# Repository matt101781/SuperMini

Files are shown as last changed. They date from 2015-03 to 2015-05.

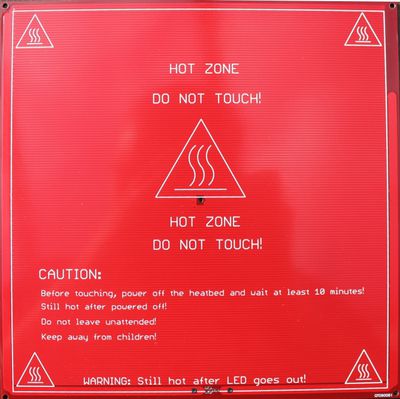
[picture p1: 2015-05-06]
cad/solidworks/decals/400px-PCB_Heatbed_MK2_front_small.jpg

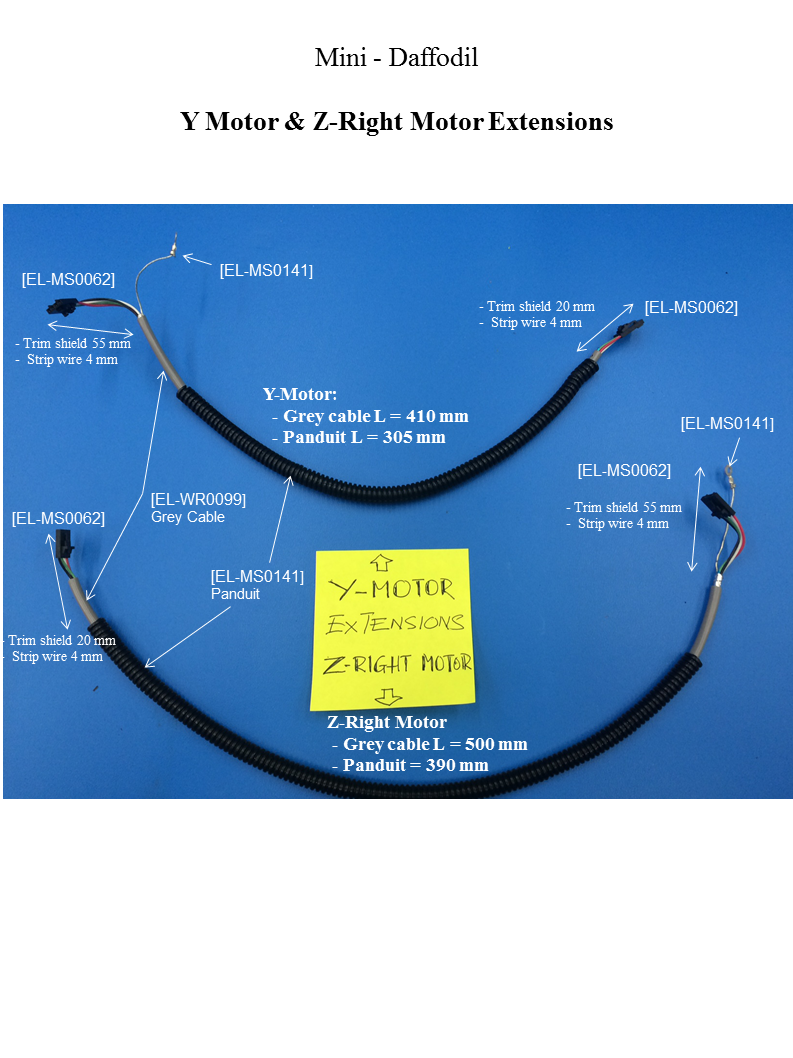
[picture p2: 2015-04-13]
electrical/mini.wire.harnesses/y&z right motor extensions.png

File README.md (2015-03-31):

# SuperMini
Super Mini - Lulzbot Clone

The super mini is a 3D printer based on the Lulzbot Mini.  
Lulzbot is a trademark of Aleph Object Inc.

Differences from the original mini:

- Sheet metal replaced with OpenBeam extruded aluminum frame.
- Bed size increased to 200x200mm.
- Firmware modified for new bed size
- Electronics replaced with TBD board.
- LCD Display added.

All of the printed parts were reused as possible.
COTS components were favored over custom machined items.

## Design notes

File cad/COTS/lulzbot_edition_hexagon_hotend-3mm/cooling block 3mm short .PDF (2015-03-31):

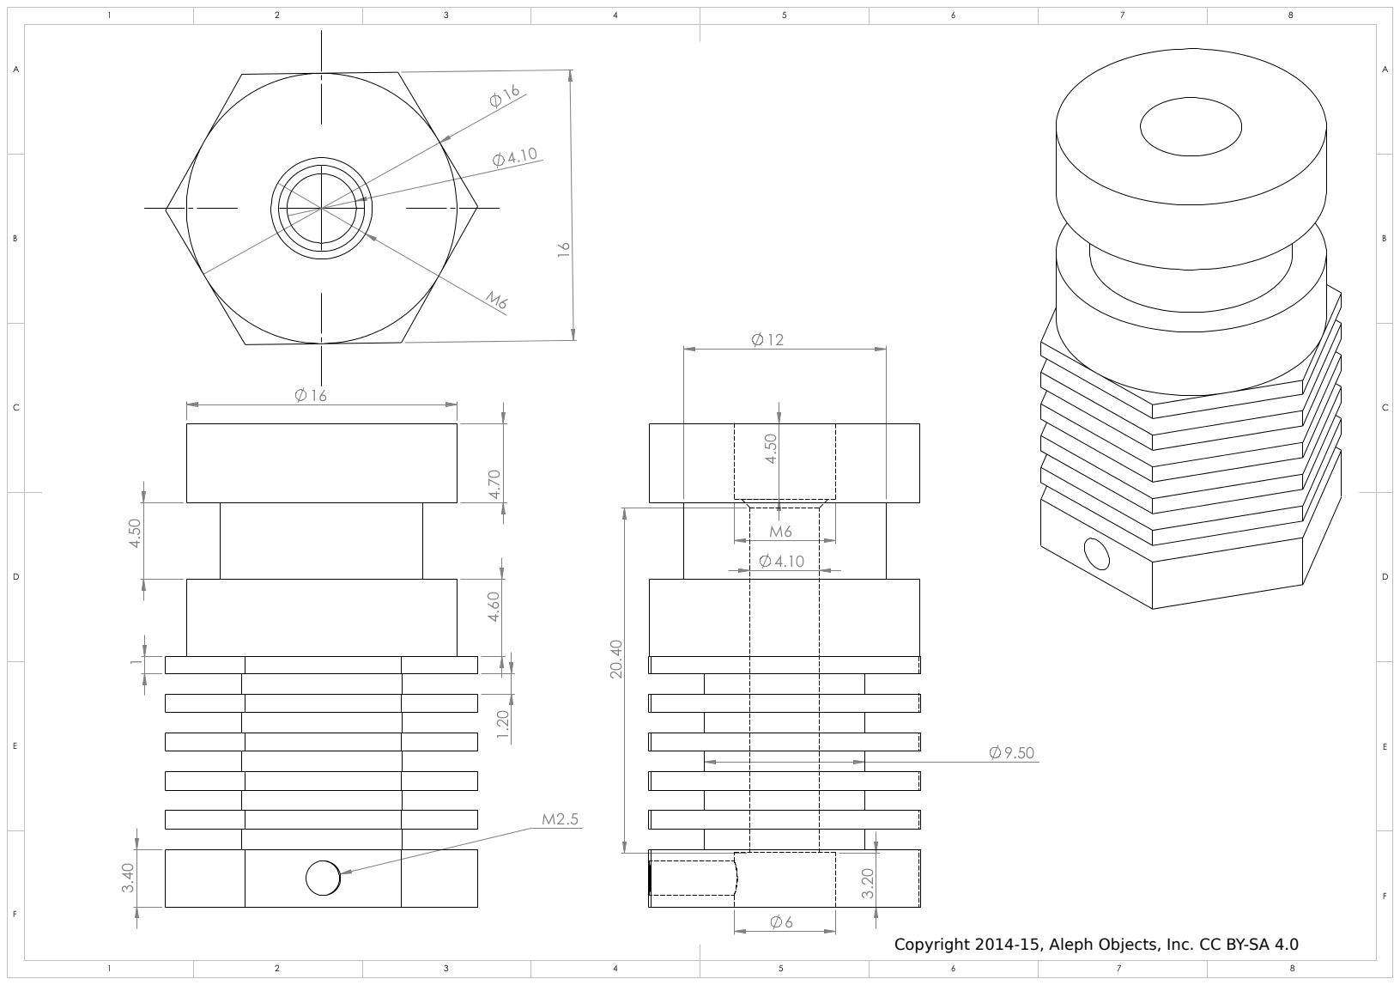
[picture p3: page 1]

Copyright 2014-15, Aleph Objects, Inc. CC BY-SA 4.0

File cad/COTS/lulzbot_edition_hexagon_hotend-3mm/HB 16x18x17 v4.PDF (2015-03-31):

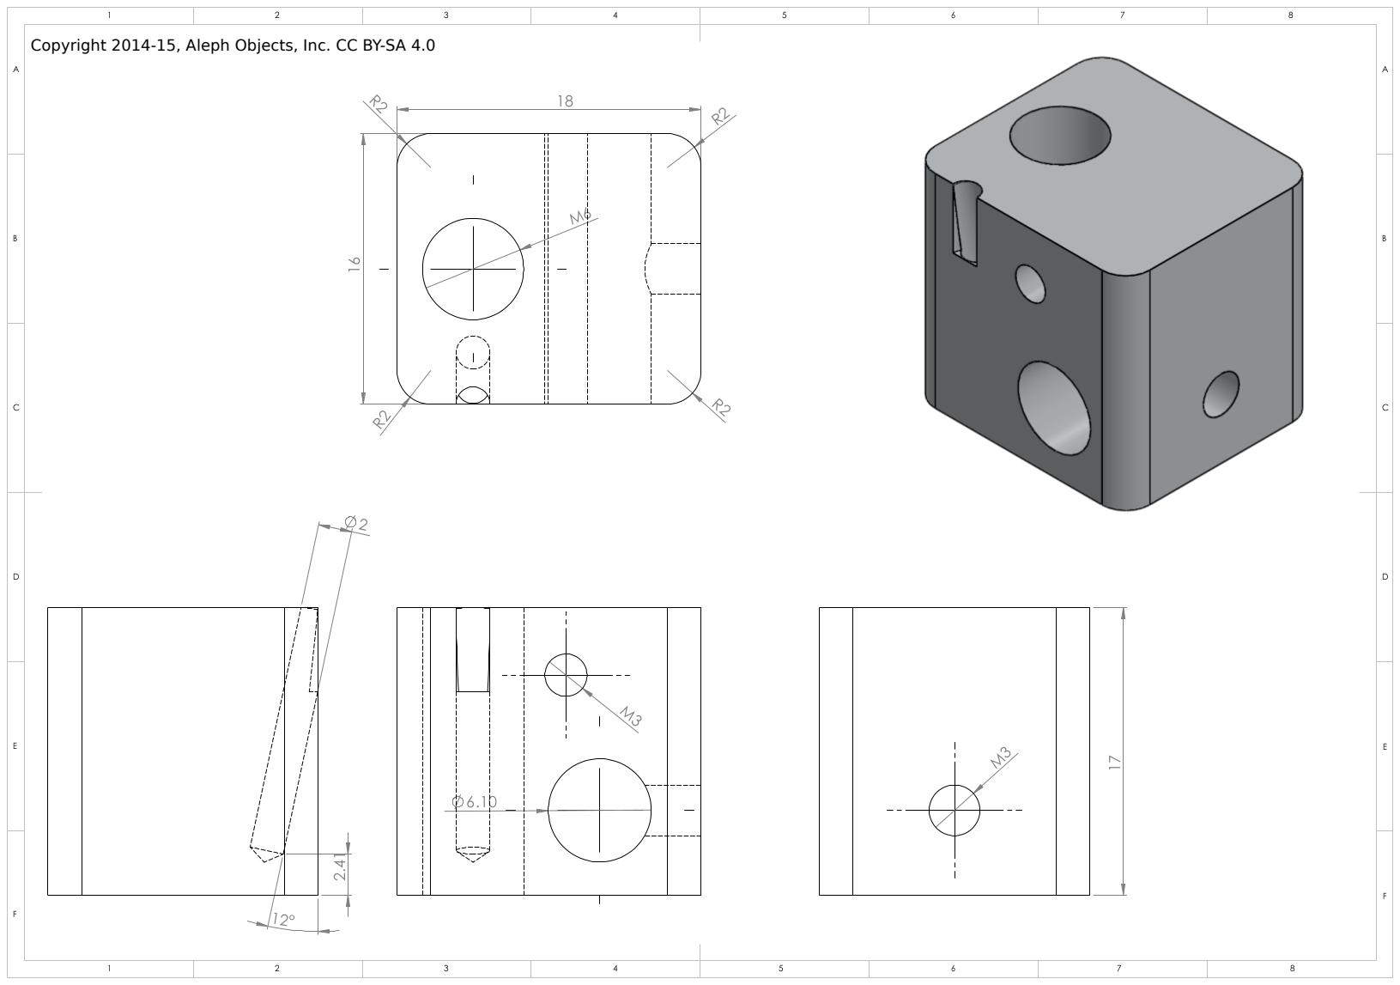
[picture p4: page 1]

Copyright 2014-15, Aleph Objects, Inc. CC BY-SA 4.0

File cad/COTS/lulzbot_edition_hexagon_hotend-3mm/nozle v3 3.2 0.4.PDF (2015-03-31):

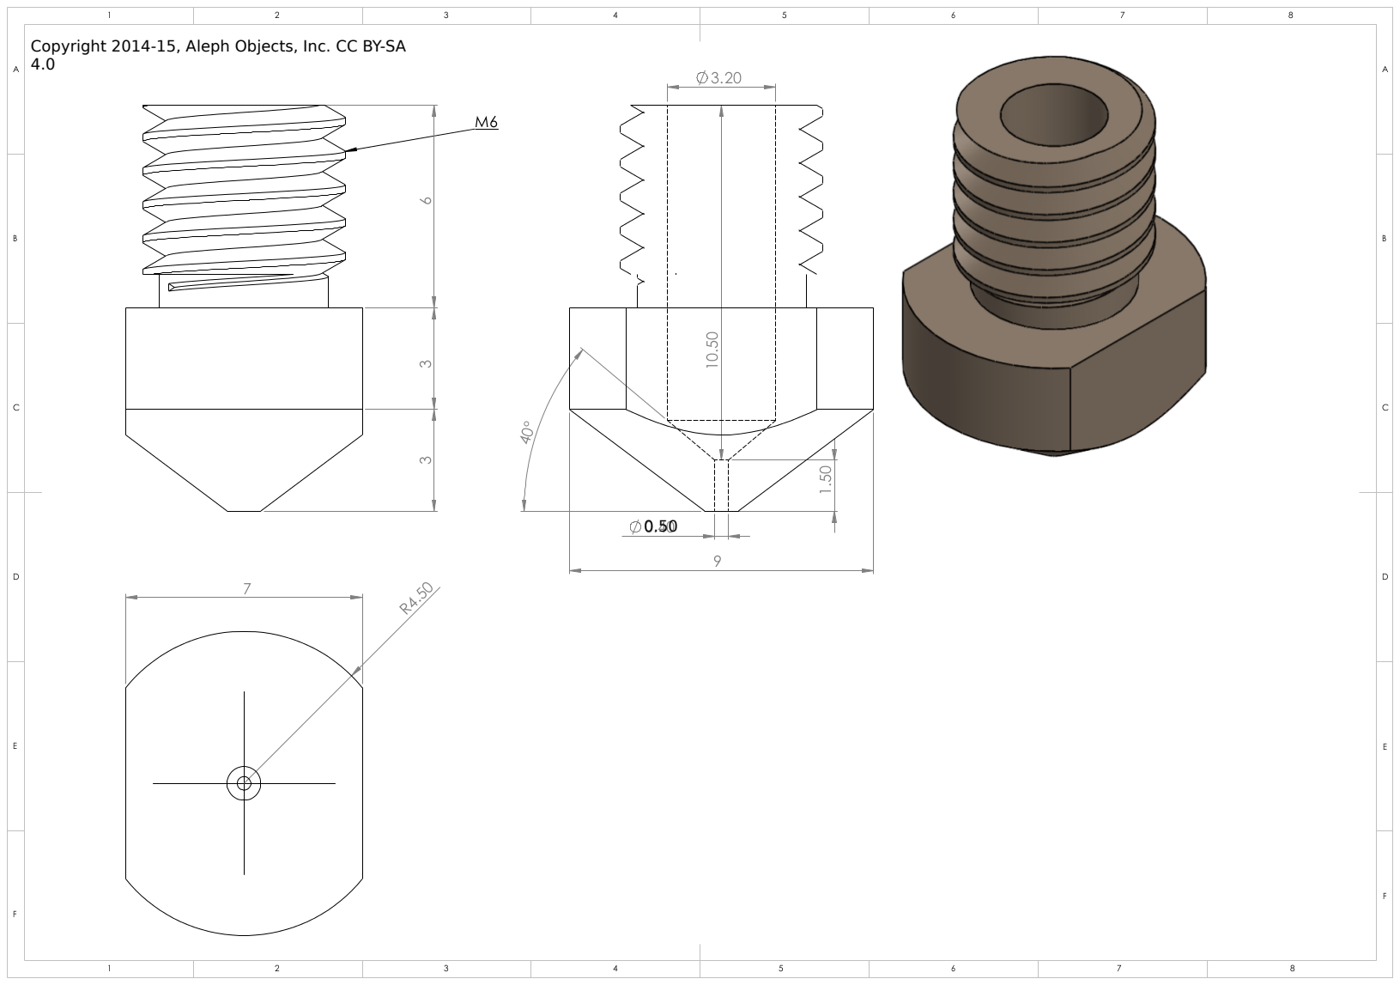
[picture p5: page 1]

0.50

Copyright 2014-15, Aleph Objects, Inc. CC BY-SA 4.0

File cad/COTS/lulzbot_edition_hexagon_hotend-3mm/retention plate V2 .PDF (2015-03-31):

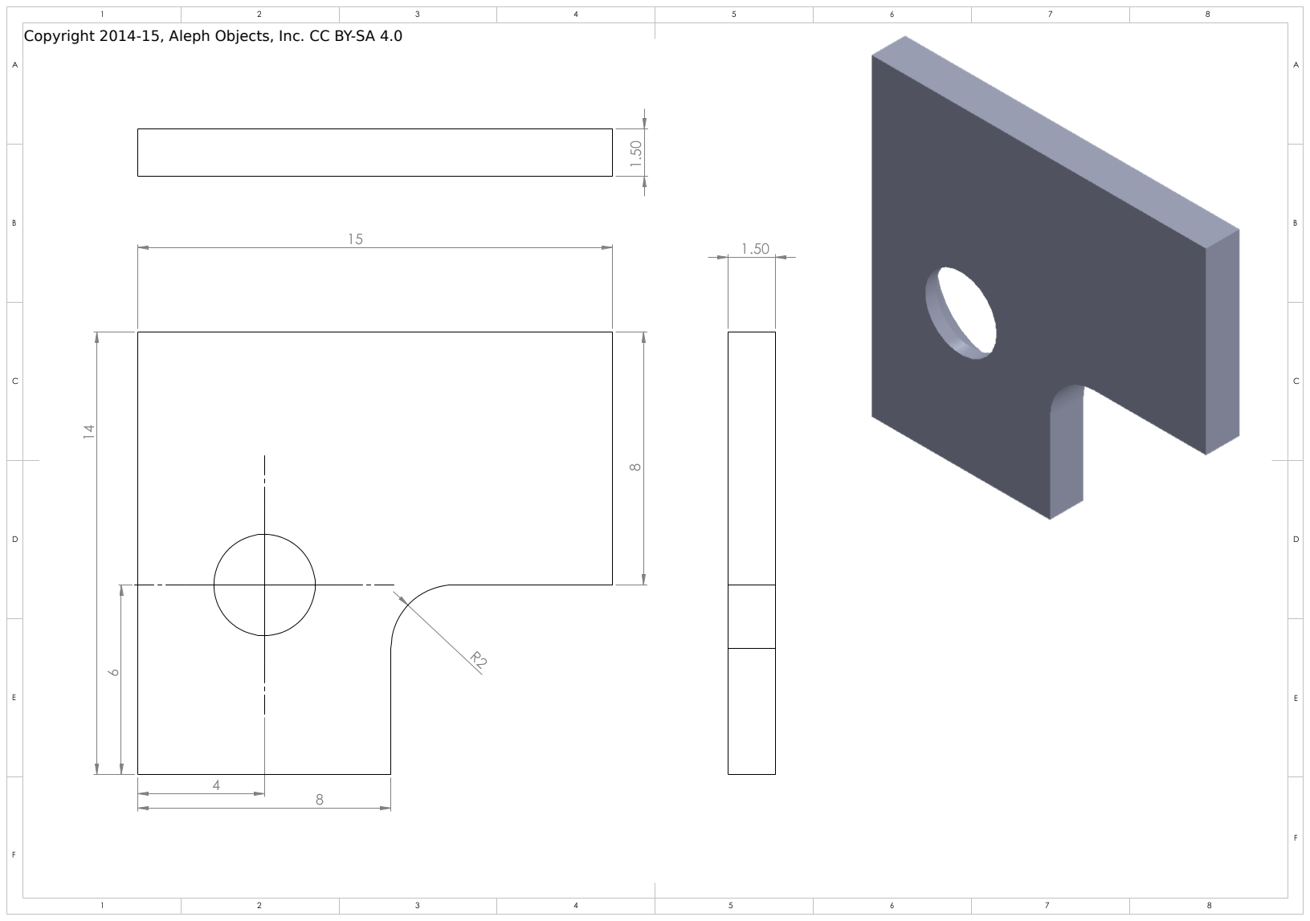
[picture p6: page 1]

Copyright 2014-15, Aleph Objects, Inc. CC BY-SA 4.0

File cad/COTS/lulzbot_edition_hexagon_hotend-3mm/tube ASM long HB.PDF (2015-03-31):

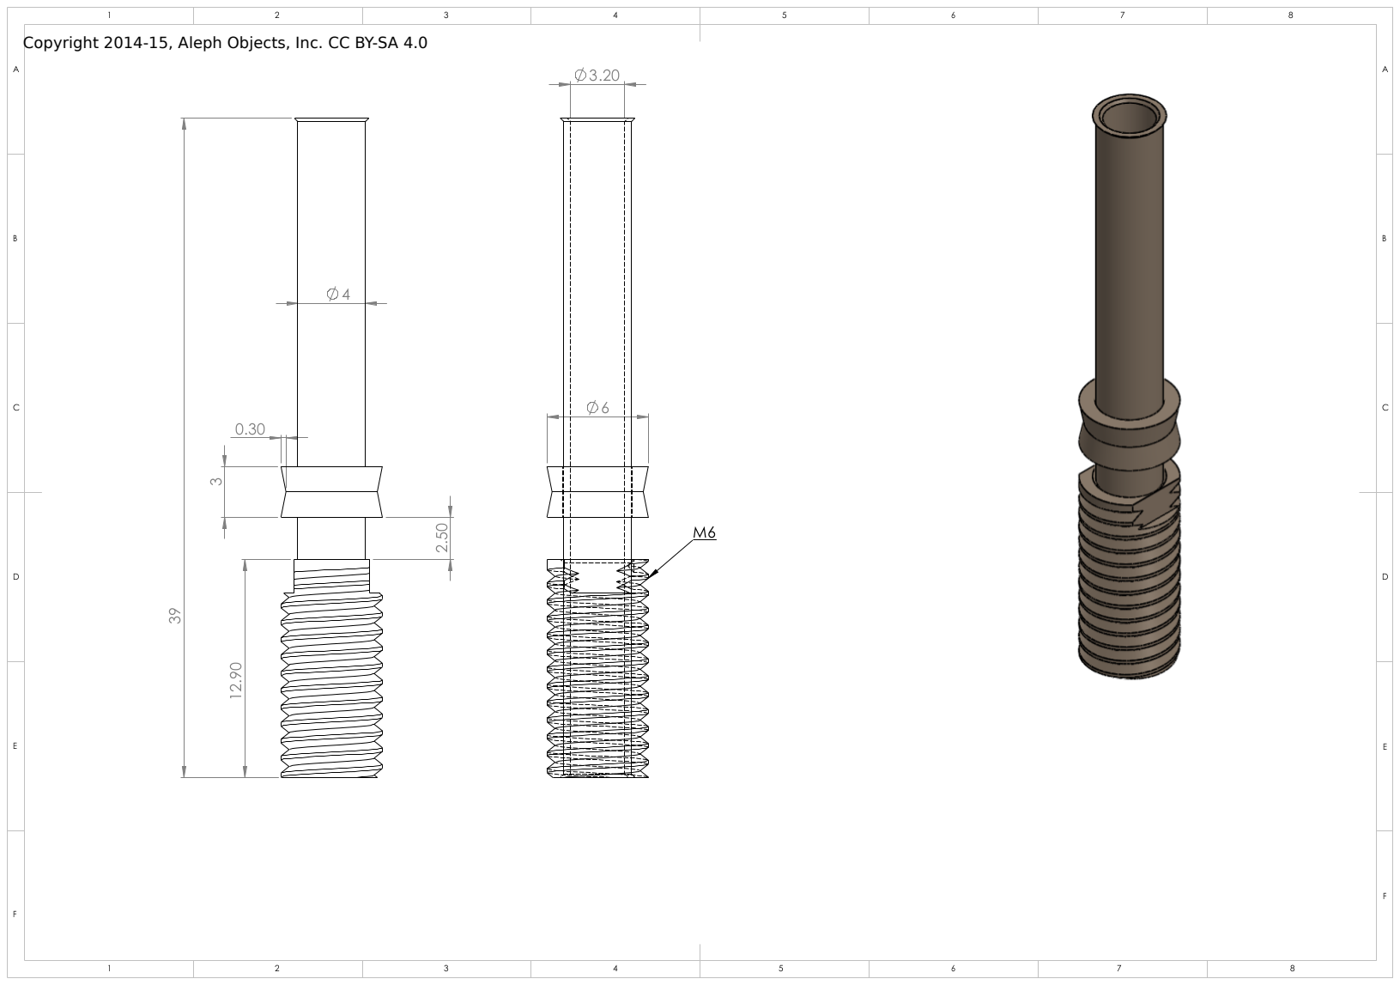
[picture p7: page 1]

Copyright 2014-15, Aleph Objects, Inc. CC BY-SA 4.0

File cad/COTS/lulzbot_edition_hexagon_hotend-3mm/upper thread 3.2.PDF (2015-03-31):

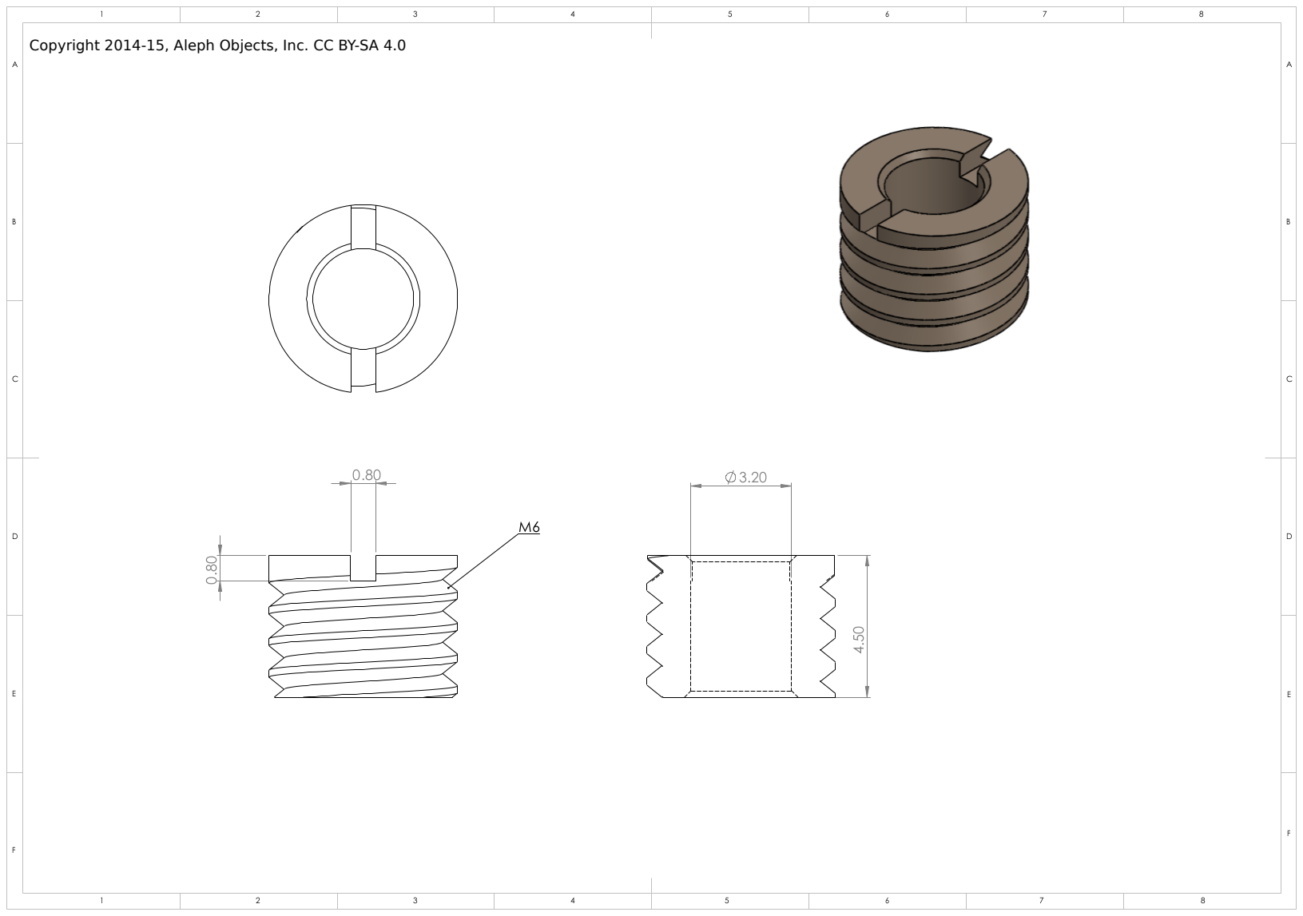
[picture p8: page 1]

Copyright 2014-15, Aleph Objects, Inc. CC BY-SA 4.0

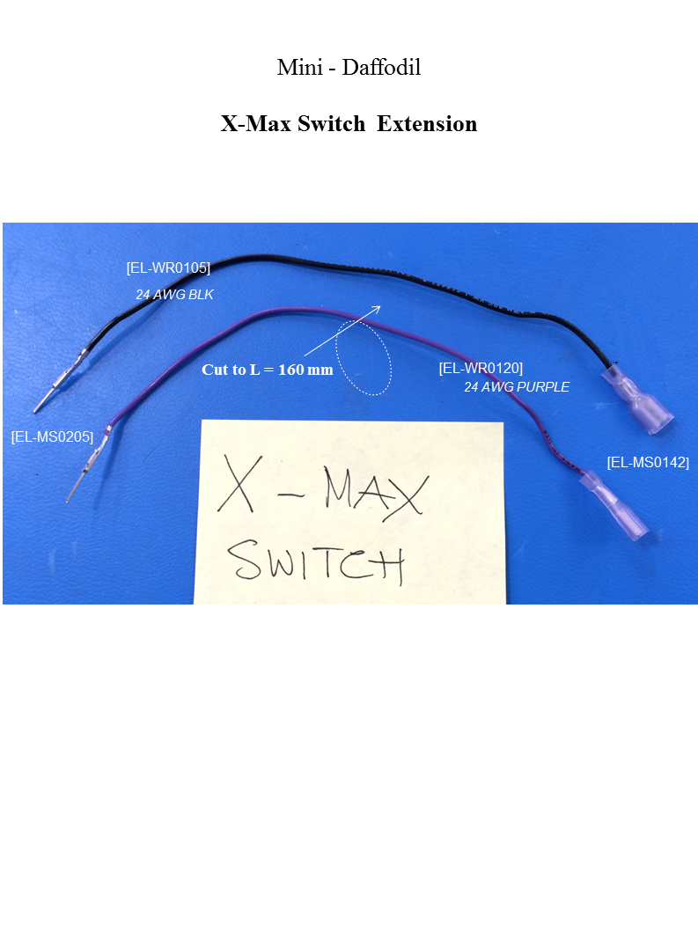
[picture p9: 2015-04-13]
electrical/mini.wire.harnesses/x max.png

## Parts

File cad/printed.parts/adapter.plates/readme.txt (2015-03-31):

Adapter Plates made with Tinkercad.

Links:

blah blah

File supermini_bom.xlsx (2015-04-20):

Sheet: BOM Summary
Supermini BOM Summary

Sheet: Linear Motion
Category | Description | Manufacturer | Manufacturer PN | Web Link | Distributor | Distributor SKU | Qty Per | UOM | My Price | Ext Price | Notes | 1000
Mechanical | DryLin® R - Solid polymer bearing RJM-01, 8mm | IGUS | RJM-01-08 |  | Direct |  | 12 | ea | $4.62 | $55.44 | Upgrade to metal bearings??
Mechanical | 8mm Smooth rod, 315mm, 304 Stainless Steel | Misumi | SSFJ8-315 |  |  |  | 2 | ea | $16.10 | $32.20 | z axis rods
Mechanical | 8mm smooth rod, 355mm, 304 Stainless Steel | Misumi | SSFJ8-355 |  |  |  | 4 | ea | $15.29 | $61.16 | x and y axis rods
Mechanical | Drive Rod 10mm | Misumi | MTSTRW10-287-F22-V7-S7-Q7-FV0-FW10-FY1 |  |  |  | 2 | ea | $56.00 | $112.00 | Get the 7MM version.
Mechanical | 10mm x 2mm Flange mount supernut | Thomson | MTS10x2m |  |  |  | 2 | ea | $25.00 | $50.00
Mechanical | Sealed Skateboard/inline/Rollerblade Skate Bearing Ball Bearings - |  |  |  | vxb.com | Kit6943 | 4 | ea | $2.12 | $8.50 | Kit of 8.
Mechanical | Metric Steel Ball Bearing, Double Sealed Bearing No.627 for 7mm Shaft Diameter |  |  |  | vxb.com |  | 4 | ea |  | $0.00 | These are for the drive rods top and bottom, changing the diameter avoids the need for these
Mechanical | Shaft Coupler 5mm to 7mm | Misumi | CPSX19-5-7 |  |  |  | 2 | ea | $26.00 | $52.00
 | NOTE - Replace 627 bearing at bottom of shaft with 636 bearing that has a 6mm bore. A 5mm to 6mm shaft coupler is then needed. -- THIS MIGHT NOT BE NECESSARY
 |  |  |  |  |  |  |  |  |  | $371.30
 | Check for LME8UU bearings, possible replacements to the poly plastic bearings

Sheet: Bed Assembly
Category | Description | Manufacturer | Manufacturer PN | Web Link | Distributor | Distributor SKU | Qty Per | UOM | My Price | Ext Price | Notes | 1000
Bed | PEI (Polyetherimide) Sheet 12" x 12" |  | ULT-0030-E | Link (http://www.amazon.com/dp/B0013HKZTA/ref=biss_dp_t_asn) | Amazon | B0013HKZTA | 1 | ea | $17.96 | $17.96
Bed | PCB Heat Bed MK2 200mm x 200mm |  |  | Link (http://www.reprapdiscount.com/electronics/14-mk2b-dual-power-heated-bed.html) | N/A |  | 1 | ea | $0.00 | $0.00 | Part of ebay kit
Bed | Borosilicate Glass Plate 213*200*3mm | Signstek |  |  | Amazon |  | 1 | ea | $17.95 | $17.95
Bed | 468MP Transfer Tape | 3M |  |  |  |  |  |  |  | $0.00
Bed | Firm White Polyester Felt Strip, 1/4" Thick, 1" Width, Plain Back, 10 ft length |  |  |  | Mcmaster | 88085K311 | 1 | ea | $4.50 | $4.50 | Bed Wiping pads
 |  |  |  |  |  |  |  |  |  | $0.00
 |  |  |  |  |  |  |  |  |  | $0.00
 |  |  |  |  |  |  |  |  |  | $0.00
 |  |  |  |  |  |  |  |  |  | $0.00
 |  |  |  |  |  |  |  |  |  | $0.00
 |  |  |  |  |  |  |  |  |  | $0.00
 |  |  |  |  |  |  |  |  |  | $40.41

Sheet: Frame
Category | Description | Manufacturer | Manufacturer PN | Web Link | Distributor | Distributor SKU | Qty Per | UOM | My Price | Ext Price | Notes | 1000
Hardware | Bumper, Rubber, 1/2" Diameter, 5/16" High, without Washer |  |  | Link (http://www.mcmaster.com/) | Mcmaster | 9540K692 | 24 | EA | $0.28 | $6.75

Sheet: Motors
Category | Description | Manufacturer | Manufacturer PN | Web Link | Distributor | Distributor SKU | Qty Per | UOM | My Price | Ext Price | Notes | 1000
Accessories | NEMA 17 Damper | Astrosyn | MY17RMDAMP | Link (http://www.ultibots.com/nema-17-damper-astrosyn-my17rmdamp/) | Ultibots | N17D | 4 | ea | $7.95 | $31.80
Motor | NEMA17 Motor |  |  |  | Lulzbot | 817752011303 | 4 | ea | $13.95 | $55.80

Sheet: Electronics
Category | Description | Manufacturer | Manufacturer PN | Web Link | Distributor | Distributor SKU | Qty Per | UOM | My Price | Ext Price | Notes | 1000
Electronics | Electronics Kit - Ebay | Various |  | Link (http://www.ebay.com/itm/331224153112?_trksid=p2060353.m1438.l2649&ssPageName=STRK%3AMEBIDX%3AIT) |  |  | 1 | EA | $90.00 | $90.00 | Contains arduino, ramps 1.4, heated bed, LCD display, GT2 pullies and belts
Electronics | SWITCH BASIC SPDT 3A .110QC 125V | Omron | SS-3GPT |  | Digikey | SW766-ND | 6 | EA | $0.95 | $5.70 | End-Stop microswitches
 | Arduino Mega |  |  |  |  |  | 1 | EA | $20.00
 | Full Graphic Smart LCD Controller | RepRapDiscount |  | Link (http://www.reprapdiscount.com/home/34-full-graphic-smart-lcd-controller.html) |  |  | 1 | EA | $69.00
 | Ramps 1.4 | RepRapDiscount |  |  |  |  | 1 | EA | $59.00

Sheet: Temp BOM
Category | Description | Manufacturer | Manufacturer PN | Web Link | Distributor | Distributor SKU | Qty Per | UOM | My Price | Ext Price | Notes | 1000
Bed | PEI Glass Bed 200mm x 200mm | Reprapdiscount |  | Link (http://www.reprapdiscount.com/mechanics/65-pei-plate.html) |  |  | 1 | ea | $35.00 | $35.00
Bed | PCB Heat Bed MK2 200mm x 200mm | Reprapdiscount |  | Link (http://www.reprapdiscount.com/electronics/14-mk2b-dual-power-heated-bed.html) |  |  | 1 | ea | $29.00 | $29.00
Bed | Metric Aluminum Unthreaded Spacer, 4.5mm OD, 8mm Length, M3 Screw Size |  |  |  | Mcmaster | 94669A615 | 4 | ea |  | $0.00
Bed | Bed leveling washer, 303 SST |  |  |  | MBK |  | 4 | ea |  | $0.00
Bed | Silicon Heater, 24V, 168mm x 168mm, Self Adhesive, w/ connectors |  |  |  | National Plastic Heater |  | 1 | ea |  | $0.00
Bed | Ultem PEI, 0.010" x 12" x 90ft rolls |  |  |  | Professional Plastics |  | 160 | mm |  | $0.00
Mechanical | GT2, Single sided Neoprene Belt | Adafruit | 1184 | Link (http://www.adafruit.com/products/1184) |  |  | 2 | ea | $9.95 | $19.90
Mechanical | GT2 Timing Pulley, 16-teeth, 5mm Bore Aluminum | Reprapdiscount |  | Link (http://www.reprapdiscount.com/home/44-gt2-pulley.html) |  |  | 2 | ea | $4.00 | $8.00
Electronic | Power Supply - 24VDC Minimum 150W |  |  |  |  |  | 1 | ea | $0.00 | $0.00 | Using acpoian power supply found during dumpster dive.
Electronic | Conn Fast Receptacle14-16 AWG .250 |  |  |  | TTI | 22-26AWG .110 | 7 | ea |  | $0.00
Electronic | CONN TERM MALE 22-24AWG TIN | Molex |  |  | Digikey / TTI | WM2517TR-ND | 45 | ea |  | $0.00
Electronic | CONN PIN 24-30AWG CRIMP TIN | Molex | 16-02-0108 |  | Heilind | MOL16-02-0108 | 2 | ea |  | $0.00 | Digi-Key part number WM2565-ND
Electronic | CONN TERM FEMALE 22-24AWG TIN | Molex Inc. | 16-02-0102 |  | Digikey / TTI | WM2510TR-ND | 93 | ea |  | $0.00
Electronic | Connector, 4 pin Male housing with latch | Molex | 701070003 |  | Digikey | WM2535-ND | 4 | ea |  | $0.00
Electronic | Connector, 4 pin Female housing with latch | Molex | 50579404 |  | Digikey | WM2902-ND | 9 | ea |  | $0.00
Electronic | CONN HOUSING 2POS .100 W/LATCH |  | 50579402 |  | TTI | WM2900-ND | 5 | ea |  | $0.00
Electronic | Connector Housing 3POS .100 W/Latch |  |  |  | TTI | WM2901-ND | 6 | ea |  | $0.00
Electronic | CONN RECEPT FASTON 22-26AWG .110 |  |  |  | TTI | A27793-ND | 12 | ea |  | $0.00
Electronic | Term Ring Non Ins 26-22AWG #4 |  | P22-4R-M |  | Heilind | P22-4R-M | 6 | ea |  | $0.00 | Digi-Key part number 298-10067-ND
Electronic | CONN RING UNINS 15-20AWG #M3 |  | 160344-2 |  | Digikey | A107160CT-ND | 2 | ea |  | $0.00
Electronic | SWITCH BASIC SPDT 3A .110QC 125V |  |  |  | Digikey | SW766-ND | 6 | ea |  | $0.00
Electronic | Shielded 4Cond 22AWG |  | C0762A.41.10 |  | Digikey | W504-1000-ND | 2490 | mm |  | $0.00
Electronic | 24AWG Stranded – Black |  | C2015A.21.01 |  | Digikey / Allcable | C2015B-1000-ND | 8735 | mm |  | $0.00
Electronic | 24AWG Stranded – White |  | C2015A.21.02 |  | Digikey / Allcable | C2015W-1000-ND | 2350 | mm |  | $0.00
Electronic | 24AWG Stranded – Yellow |  | C2015A.21.05 |  | Digikey | C2015Y-1000-ND | 2150 | mm |  | $0.00
Electronic | 24AWG Stranded – Red |  | C2015A.21.03 |  | Digikey / Allcable | C2015R-1000-ND | 5200 | mm |  | $0.00
Electronic | 24AWG Stranded – Orange |  | C2015A.21.04 |  | Digikey | C2015A-1000-ND | 3000 | mm |  | $0.00
Electronic | 24AWG Stranded – Blue |  | C2015A.21.07 |  | Digikey | C2015L-1000-ND | 550 | mm |  | $0.00
Electronic | 24AWG Stranded – Green |  | C2015A.21.06 |  | Digikey / Allcable | C2015G-1000-ND | 1800 | mm |  | $0.00
Electronic | 24AWG Stranded – Purple |  | C2015A.21.19 |  | Digikey | C2015V-1000-ND | 1310 | mm |  | $0.00
Electronic | 16AWG Stranded – Red |  | C2065A.21.03 |  | Digikey | C2065R-1000-ND | 400 | mm |  | $0.00
Electronic | 16AWG Stranded – Black |  | C2065A.21.01 |  | Digikey / Allcable | C2065B-1000-ND | 1270 | mm |  | $0.00
Electronic | 16AWG Stranded – Green |  | C2065A.21.06 |  | Digikey | C2065G-1000-ND | 130 | mm |  | $0.00
Electronic | 16AWG Stranded – White |  | C2065A.21.02 |  | Digikey / Allcable | C2065W-1000-ND | 870 | mm |  | $0.00
Electronic | 16AWG Stranded – Violet |  | C2065A.12.19 |  | Digikey | C2065V-1000-ND | 1100 | mm |  | $0.00
Electronic | Ferrite Tubular Bead 19.00mm | Laird Technologies - Signal Integrity Products | 28B1142-100 |  | Digikey / Sager | 240-2314-ND | 6 | ea |  | $0.00
Electronic | FERRIT CYLINDR BOX CLAMP.350"WHT | Laird Technologies - Signal Integrity Products | 28A2029-0A0 |  | Digikey | 240-2076-ND | 1 | ea |  | $0.00
Electronic | Term Block Plug 4POS STR 5.08MM |  |  |  | Digikey | WM7953-ND | 1 | ea |  | $0.00
Electronic | Term Block Plug 2POS STR 5.08MM |  |  |  | TTI | WM7819-ND | 2 | ea |  | $0.00
Electronic | 20-POS .100 Dual (Black) |  |  |  | Digikey | WM2527-ND | 2 | ea |  | $0.00
Electronic | REEL – RING TONGUE CONN 16-22 AWG #10 PIDG | TE | 2-36154-2 |  | Digikey / TTI | A1062TR-ND | 7 | ea |  | $0.00
Hot End | Lulzbot Mini Hot End | Lulzbot | 817752016186 | Link (https://www.lulzbot.com/products/lulzbot-mini-tool-head) |  |  |  |  | $175.00 | $0.00
Hot End | Reprap Modified Hexagon Hotend, Lulzbot Edition, 3.0mm Filament |  |  |  | Reprapdiscount |  | 1 | ea |  | $0.00
Hot End | FAN,24VDC,Sleeve,5.75CFM,40X40X10MM,60mA 6000RPM,1.44W,280MM LEADS,CE/RoHS |  | TF4010-24H-S |  | Kysan |  | 1 | ea |  | $0.00
Hot End | FAN,24VDC,BALL,31.60CFM,80×80×15 MM,100mA |  | TF8015-24M-B |  | Kysan | 69866 | 1 | ea |  | $0.00
Hot End | Hobbed Bolt, M8 x 50mm Hex head, 26mm offset, Stainless Steel |  |  |  | Quattro |  | 1 | ea |  | $0.00
Hot End | 8mm Smooth Rod x 18-19mm |  |  |  | MBK |  | 1 | ea |  | $0.00
Hot End | Extreme-Temperature Pipe Sealant & Threadlocker, 4 oz bottle, blue |  |  |  | Mcmaster | 7604A55 | 0.5 | g |  | $0.00
Hot End | RFB2008 Micro Blower with 30awg wire that is 250mm long |  |  |  | Pelonis |  | 1 | ea |  | $0.00
Hot End | Thumb Screw Knob for M4 SHCS, Black |  |  |  | Timberline |  | 2 | ea |  | $0.00 |  | Mcmaster | 91175A062
Hot End | M2 x 6 SHCS, Black-Oxide |  |  |  | Timberline |  | 1 | ea |  | $0.00
Hot End | Metric Spring Steel Shim - DIN 988 0.5mm Thick, 8mm ID, 14mm OD |  |  |  | Timberline |  | 1 | ea |  | $0.00 |  | Mcmaster | 98055A114
Hot End | Metric Spring Steel Shim - DIN 988 1.0mm Thick, 8mm ID, 14mm OD |  |  |  | Timberline |  | 1 | ea |  | $0.00 |  | Mcmaster | 98055A115
Hardware | Snap-Together Cable and Hose Carrier, Feed-Through, 0.41" High x 0.39" Wide Interior Size |  |  |  | IGUS | 06-10-028-0 | 813 | mm |  | $0.00
Hardware | Mounting Brackets for .41" High x .39" Wide Interior Snap-Together Cable and Hose Carrier |  |  |  | IGUS | 060-10-12 | 3 | ea |  | $0.00
Mechanical | DryLin® R - Solid polymer bearing RJM-01, 8mm |  |  |  | IGUS | RJM-01-08 | 12 | ea |  | $0.00
Mechanical | 8mm Smooth rod, 315mm, 304 Stainless Steel |  |  |  | MBK |  | 6 | ea |  | $0.00
Electronic | EMI/RFI-Shield Heat-Shrink Tubing 3/16" ID Before, 3/32" ID After, 48" L, Black | Techflex | H2C0.19BK |  | Allcable | H2C0.19BK | 450 | mm |  | $0.00 |  | Mcmaster 7937K31
Electronic | Interference-Shielding Heat-Shrink Tubing, 3/8" ID Before, 3/16" ID After, 48" Long, Black | Techflex | H2C0-38BK |  | Allcable | H2C0-38BK | 125 | mm |  | $0.00 |  | Mcmaster 7937K33
Hardware | Metric 18-8 Stainless Steel External Serrated Lock Washer, M3 Screw Size, 6mm OD, 0.4mm min Thick |  |  |  | Mcmaster | 91120A120 | 4 | ea |  | $0.00
Hardware/tools | Firm White Polyester Felt Strip, 1/4" Thick, 1" Width, Plain Back |  |  |  | Mcmaster | 88085K311 | 270 | mm |  | $0.00 | The wiper pads
Electronic | Tubing, Corrugated Loom .25" | Panduit | 708161 |  | Fastenal | 708161 | 695 | mm |  | $0.00
Hardware | Black Alloy Steel Flat-Head Socket Cap Screw, Class 10.9, M8 Size, 40mm Length, 1.25mm Pitch |  |  |  | Timberline |  | 1 | ea |  | $0.00 |  | Mcmaster | 91294A289
Hardware | Black Alloy Steel Flat-Head Socket Cap Screw, Class 10.9, M8 Size, 45mm Length, 1.25mm Pitch |  |  |  | Timberline |  | 1 | ea |  | $0.00 |  | Mcmaster | 91294A290
Hardware | Metric Brass Heat-Set Insert for Plastics, Tapered, M2-.4 Internal Thread, 2.9MM Length |  |  |  | Mcmaster / Hayden Industrial | 94180A307 | 13 | ea |  | $0.00 |  | Mcmaster | 94180A307
Hardware | Metric Class 12.9 Socket Head Cap Screw Alloy Steel, Black, M2 Thread, 10mm Length, 0.4mm Pitch |  |  |  | Fastenal |  | 12 | ea |  | $0.00 |  | Mcmaster | 91290A017
Hardware | Steel Flat Washer, DIN 125 zinc-plated class 4,M2 screw sz, 5mm OD, .25mm-.35mm thick |  | 40350 |  | Fastenal | 40350 | 12 | ea |  | $0.00 |  | Mcmaster | 91166A180
Hardware | M3-.5 3.8mm Heatset Insert |  | 11125995 |  | Fastenal | 11125995 | 79 | ea |  | $0.00 |  | Mcmaster | 94180A331 (As of 09/17/2014 they have a 2 week lead time on this part. I don't want to fill in because Fastenal Rep is hoping to get units from the Manufacturer sooner, just can't promise
Hardware | M5-.8 6.7mm Heatset Insert |  | 11125997 |  | Fastenal | 11125997 | 13 | ea |  | $0.00 |  | Mcmaster | 94180A361 - As of 09/17/2014 they have a 2 week lead time on this part. I don't want to fill in because Fastenal Rep is hoping to get units from the Manufacturer sooner, just can't promise
Hardware | M3 Nyloc Nut, Zinc Plated |  |  |  | Timberline / McMaster | 90576A102 | 7 | ea |  | $0.00 |  | Mcmaster | 90576A102
Hardware | M3 Nut, Zinc Plated |  |  |  | Timberline |  | 3 | ea |  | $0.00 |  | Mcmaster | 90591A121
Hardware | M3 Set Screw (Grub Screw) |  | NS0310-0306/met |  | Mcmaster | 91390A100 | 7 | ea |  | $0.00 |  | Mcmaster | 91390A100
Hardware | M3 Washer, Steel, Zinc Plated |  | 91166A210 |  | Timberline / McMaster | MTR-M3100321 | 73 | ea |  | $0.00 |  | Mcmaster | 91166A210
Hardware | M3 x 5 Bolt, SHCS Black-Oxide | 39501 | 39501 |  | Fastenal | 39501 | 4 | ea |  | $0.00
Hardware | M3 x 6 Bolt, BHCS Black-Oxide |  |  |  | Mcmaster | 91239A111 | 12 | ea |  | $0.00
Hardware | M3 x 6 Bolt, FHCS Black-Oxide |  |  |  | mcmaster | 91294A126 | 85 | ea |  | $0.00 |  | Mcmaster | 91294A126
Hardware | M3 x 8 Bolt, BHCS, SST |  |  |  | mcmaster | 92095A181 | 3 | ea |  | $0.00 |  | Mcmaster | 92095A181
Hardware | M3 x 8 Bolt, BHCS, Black-Oxide |  |  |  | mcmaster | 91239A113 | 19 | ea |  | $0.00 |  | Mcmaster | 91239A113
Hardware | M3 x 12 Bolt, SHCS Black-Oxide |  |  |  | Timberline | 8050-0312 | 45 | ea |  | $0.00 |  | Mcmaster | 91290A117
Hardware | M3 x 14 Bolt FHCS, Black-Oxide |  |  |  | mcmaster | 91294A133 | 2 | ea |  | $0.00 |  | Mcmaster | 91294A133
Hardware | M3 x 12 Bolt FHCS, SST |  |  |  | Timberline |  | 4 | ea |  | $0.00 |  | Mcmaster | 92125A132
Hardware | M3 x 25 Bolt FHCS, Black-Oxide |  |  |  | mcmaster | 91294A138 | 4 | ea |  | $0.00
Hardware | M3 x 25 Bolt, SHCS Black-Oxide |  | 91290A125 |  | mcmaster | 8050-0325 | 1 | ea |  | $0.00 |  | Mcmaster | 91290A125
Hardware | M4 Nut,Zinc-Plated Steel |  |  |  | Timberline | 8100-0040 | 4 | ea |  | $0.00 |  | Mcmaster | 90591A141
Hardware | M4 Washer |  |  |  | Timberline | 8200-0040 | 6 | ea |  | $0.00 |  | Mcmaster | 91166A230
Hardware | M4 x 25 Bolt, SHCS Black-Oxide |  |  |  | mcmaster | 91290A176 | 2 | ea |  | $0.00 |  | Mcmaster | 91290A176
Hardware | M4 x 55 Bolt, SHCS Black-Oxide |  |  |  | Timberline | NS8050-0455 | 2 | ea |  | $0.00 |  | Mcmaster | 91290A187
Hardware | M5 Washer, Steel, Zinc Plated |  |  |  | mcmaster | 91166A240 | 11 | ea |  | $0.00 |  | Mcmaster | 91166A240
Hardware | M5 x 10 Bolt, SHCS Black-Oxide |  |  |  | Timberline | 8050-0510 | 6 | ea |  | $0.00 |  | Mcmaster | 91290A224
Hardware | M5 x 14 Bolt, SHCS Black_Oxide |  |  |  | Timberline | NOR-M60051014SO | 5 | ea |  | $0.00
Hardware | M8 Nyloc Nut, Zinc Plated |  |  |  | Timberline | GBO-986270004 | 3 | ea |  | $0.00 |  | Mcmaster | 90576A117
Hardware | M8 Washer, Steel, Zinc Plated |  |  |  | Timberline | 8200-0080 | 9 | ea |  | $0.00 |  | Mcmaster | 91166A270
Hardware | Alloy Steel Shoulder Screw, 6mm Diameter x 10mm Long Shoulder, M5 Thread |  | 92981A100 |  | Mcmaster | 7130k32 | 2 | ea |  | $0.00
Hardware | UV-Resistant Cable Tie Holder, Adhesive Back/Screw Mount, 4-Way, for.18" Maximum Tie, Black |  |  |  | Mcmaster | 7582k22 | 6 | ea |  | $0.00
Mechanical | Drive Rod 10mm (Rev. B) |  |  |  | Thomson |  | 2 | ea | $56.00 | $112.00 | Possibly machine from Mcmaster p/n 7549K1 Misui P/N for machined part: MTSTRW10-287-F7-V7-S22-Q7-FV0-FW10-FY1 -- Requires 10mm to 5mm coupler
Mechanical | 10mm x 2mm Flange mount supernut |  | MTS10 x 2m |  | Thomson |  | 2 | ea |  | $0.00 | Possible replacement - MTSFR10 - requires changes to printed part
Mechanical | Coupling, Set Screw, Misumi GSASL16-5-5 |  |  |  | Misumi | GSASL16-5-5 | 2 | ea |  | $0.00
Mechanical | S-13994 3M 468MP Adhesive Transfer Tape - 12" x 60 yards |  |  |  | Uline | S-13994 | 160 | mm |  | $0.00
Electronic | AC Power Entry Modules SC MT FUSED .25" TAB |  |  |  | Mouser | 161-PF0030/63 | 1 | ea |  | $0.00
Electronic | Cartridge Fuses 125V 7A 5X20 MA UL LBC |  |  |  | Mouser | 576-0233007.MXP | 2 | ea |  | $0.00
Electronic | Wire - Single Conductor 20AWG SOLID PTFE, RED |  |  |  | Mouser | 602-2856/1-100-03 | 200 | mm |  | $0.00
Electronic | Heavy Duty Power Connectors HOUSING ONLY, BLACK POWERPOLE 15/45 |  |  |  | Mouser | 879-1327G6-BK | 2 | ea |  | $0.00
Electronic | Heavy Duty Power Connectors POWERPOLE 15A CONT |  |  |  | Mouser | 879-1332-BK | 2 | ea |  | $0.00
Electronic | SWITCH ROCKER DPST 20A 250V, illuminated red | E-Switch | R5BBLKREDFF2 |  | Digikey | EG1535-ND | 1 | ea |  | $0.00
Electronic | NEMA 17 Stepper Motors |  |  |  | Changzhou FTX Motors Co., Ltd. | SY42STH47-1504A | 5 | ea | $13.95 | $69.75 | 55 N/m, 1.8 deg, 2.8V, lulzbot branded ones probably best option.
 |  |  |  |  |  |  |  |  |  | $0.00
Electronic | Mini RAMBo 1.1b, assembled board only |  |  |  | UltiMachine |  | 1 | ea |  | $0.00 | Look into possible alternatives. RAMPS board is $60 at reprapdiscount
 |  |  |  |  |  |  |  |  |  | $0.00
Mechanical | Sealed Skateboard/inline/Rollerblade Skate Bearing Ball Bearings |  |  |  | vxb.com | Kit708 | 7 | ea |  | $0.00
Mechanical | Metric Steel Ball Bearing, Double Sealed Bearing No.627 for 7mm Shaft Diameter |  |  |  | vxb.com |  | 4 | ea |  | $0.00
 |  |  |  |  |  |  |  |  |  | $273.65
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

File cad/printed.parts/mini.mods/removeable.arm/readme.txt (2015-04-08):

See https://forum.lulzbot.com/viewtopic.php?f=43&t=1994

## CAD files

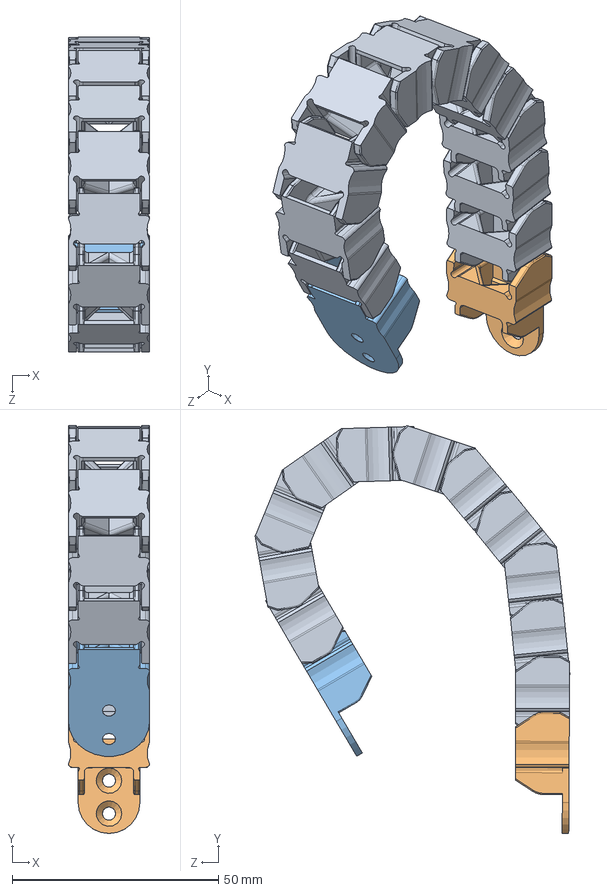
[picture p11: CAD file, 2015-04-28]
cad/solidworks/cable.chain/cable_chain.SLDASM
19.7 x 98.9 x 76.4 mm
chain_segment_ver.2 x 11
chain_start_ver.2
chain_end_ver.2

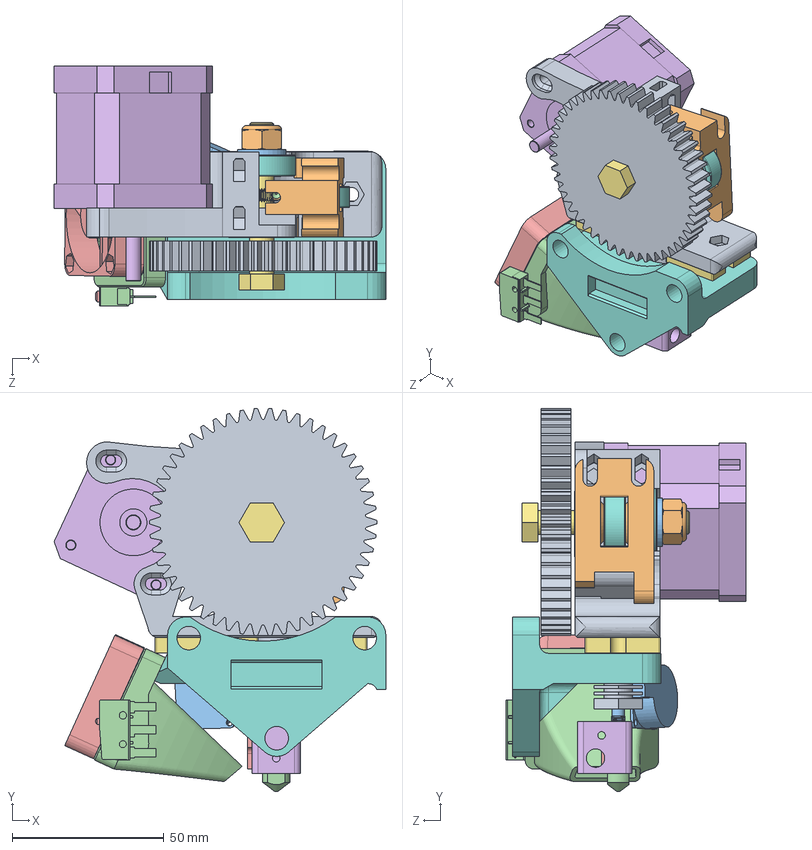
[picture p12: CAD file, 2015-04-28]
cad/solidworks/hex.nozzle/Lulzbot.Mini.COTS.Extruder.SLDASM
109.4 x 126.3 x 79.3 mm
cooling_block
upper_plug
tube_ASM
hex_nozzle
retention_plate
heating_block
hex_mount_plate
Extruder_mount_camellia_v2.4
ext_body_camellia
extruder_idler_v1.4
RFB2008_UL
fan_mount_camellia_v1.3
40mm_Fan
nema17
Hobbed_bolt_26
608.Bearing x 3
large_gear_camellia
93625A300
93475A270
SS_3GPT_BASE
SS_3GPT_ACTUATOR

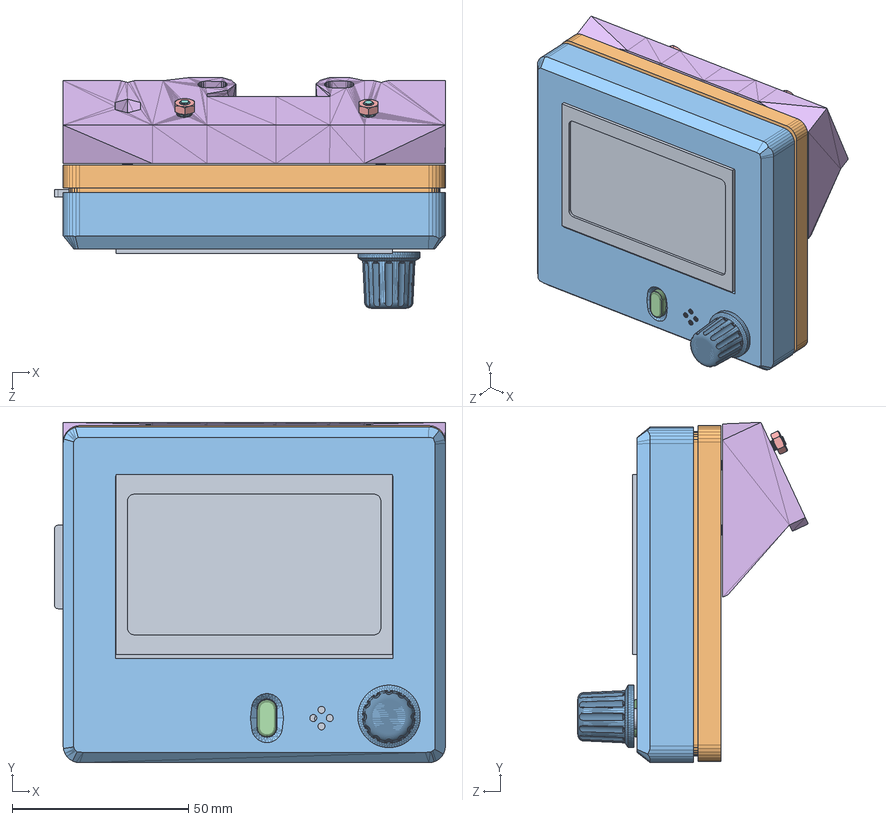
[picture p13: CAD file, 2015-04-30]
cad/solidworks/lcd/LCD.Assembly.SLDASM
111.1 x 96.7 x 65.5 mm
Full Graphic Smart Controller
LCD.Case.Bottom
LCD.Case.Top
LCD.Stop.Button
91828A211 x 5
LCD.adapter
92095A184 x 3
92095A181 x 2
93475A210 x 2
92148A150 x 2
LCD_knob_big

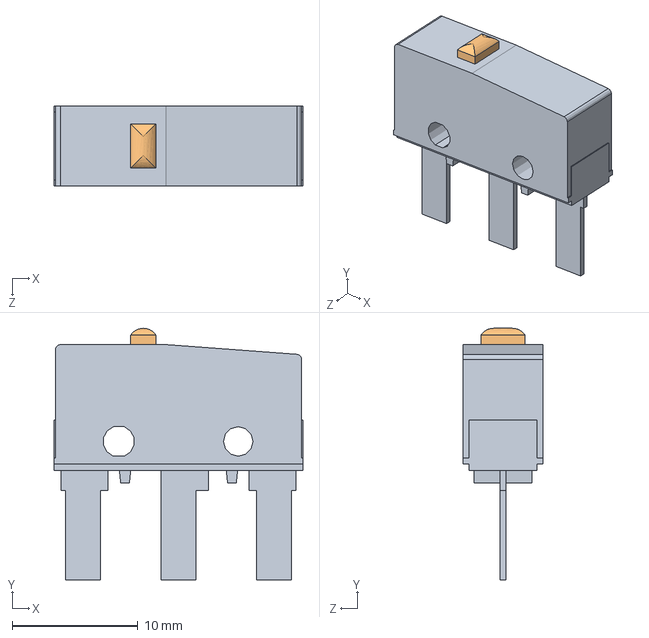
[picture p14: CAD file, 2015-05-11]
cad/solidworks/vendor.models/SS-3GPT/SS_3GPT.SLDASM
19.8 x 20.0 x 6.40 mm
SS_3GPT_BASE
SS_3GPT_ACTUATOR

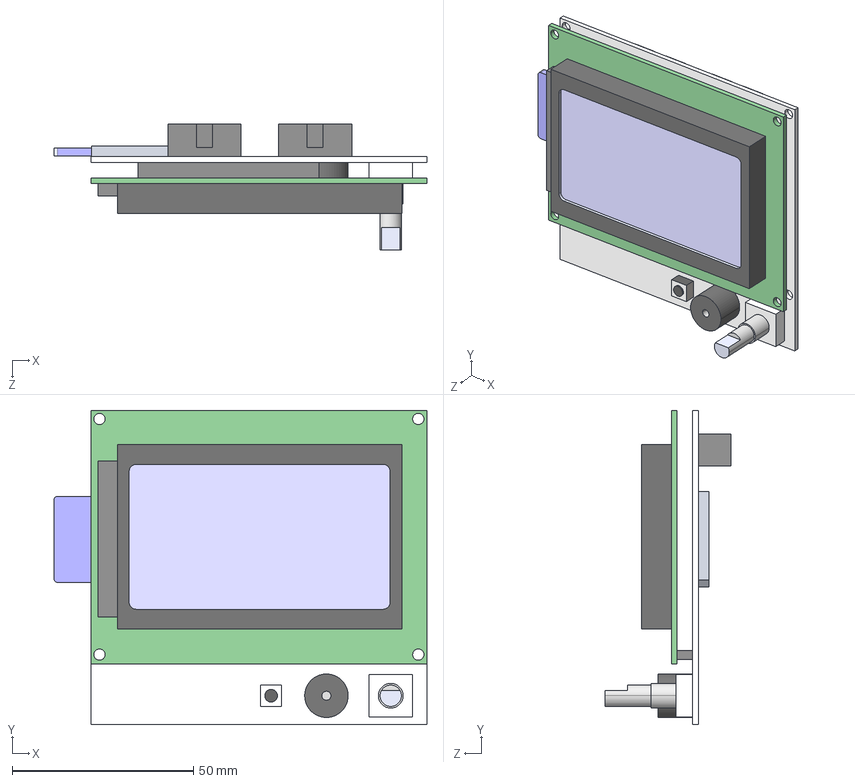
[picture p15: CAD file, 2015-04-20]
cad/solidworks/lcd/Full Graphic Smart Controller.STEP
102.9 x 86.8 x 34.7 mm

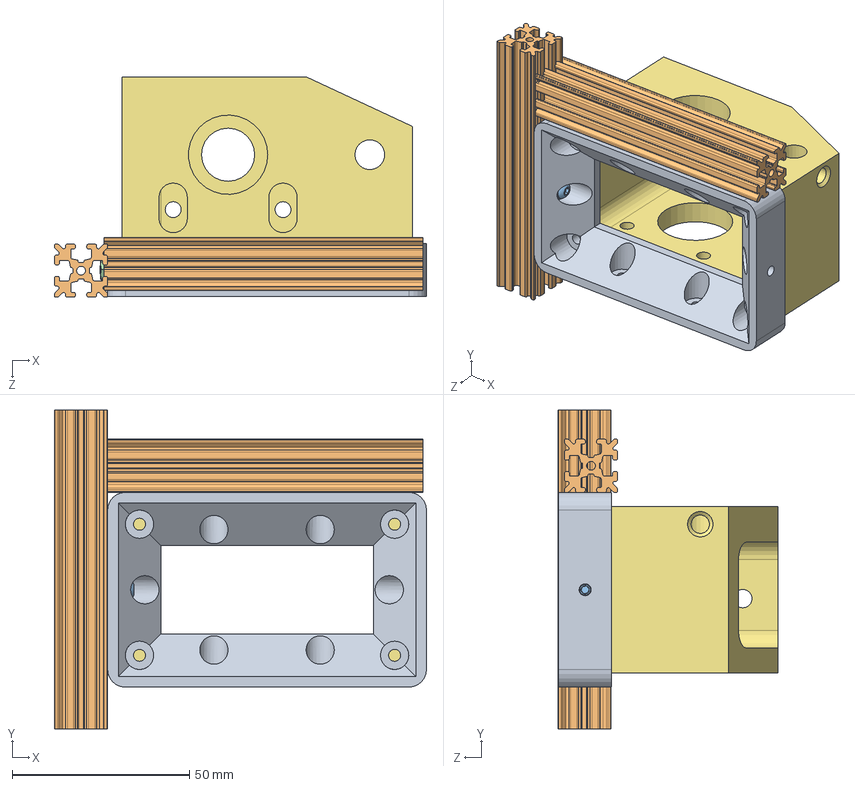
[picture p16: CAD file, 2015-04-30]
cad/solidworks/adapter.plates/adapter.plate.test.assem.SLDASM
105.0 x 90.0 x 62.2 mm
lower.z.adapter.plate.v2
open.beam.extrusion.90mm x 2
92095A181
91828A211
93475A210
92148A150
lower_z_left_camellia_v1.1

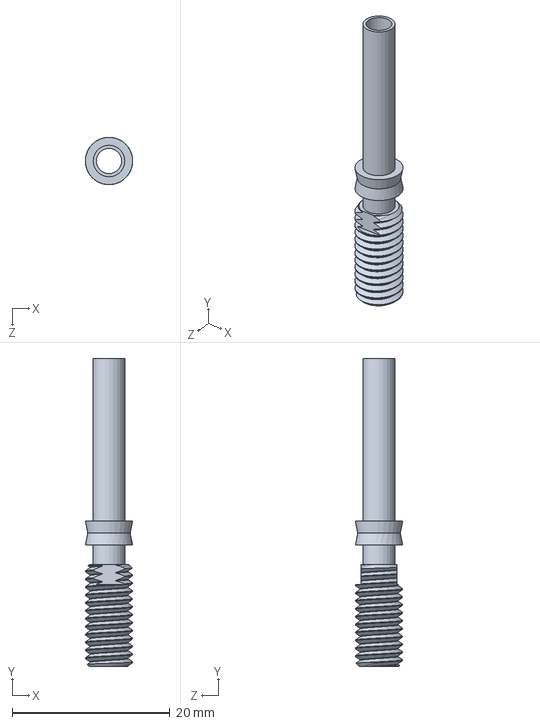
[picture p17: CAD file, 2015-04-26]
cad/solidworks/hex.nozzle/tube_ASM.SLDPRT
6.00 x 39.0 x 6.00 mm

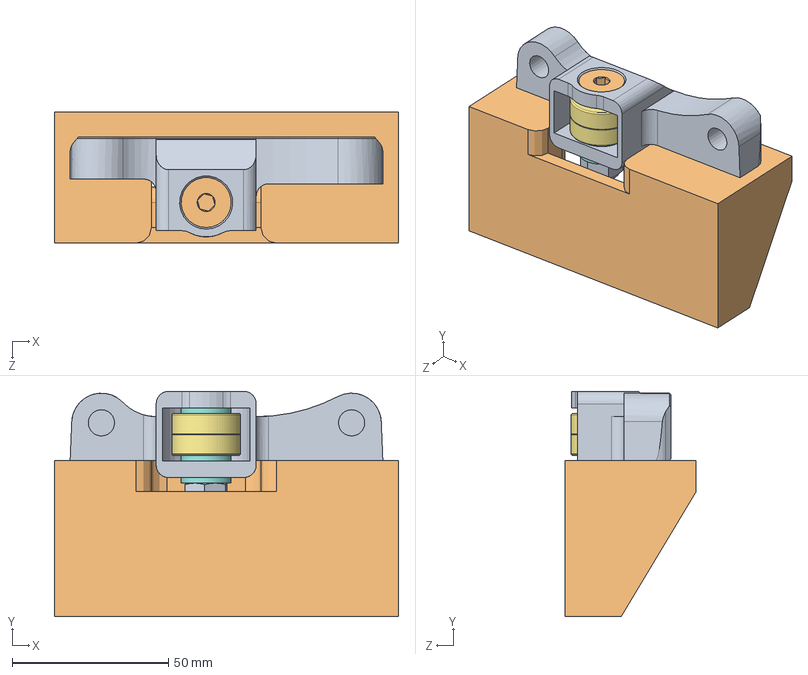
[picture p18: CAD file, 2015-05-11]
cad/solidworks/Y.Idler.Assembly.sldasm
110.0 x 72.1 x 42.0 mm
Y_end_idler_Camellia_v1.3
Y.Ilder.Mount.v2
94180A331 x 4
93475A210 x 4
92148A150 x 4
92095A182 x 4
608-ZZ Radial Ball Bearing x 2
93475A270 x 3
93625A300
92125A294

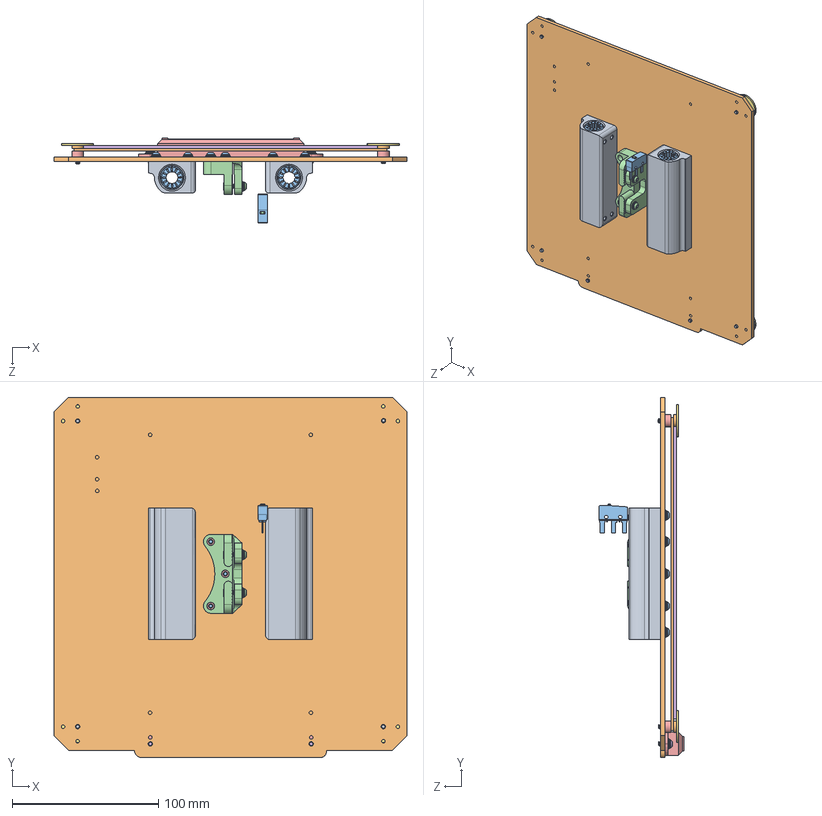
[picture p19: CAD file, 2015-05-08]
cad/solidworks/Bed.Assembly.sldasm
241.4 x 246.4 x 58.3 mm
double_bearing_holder_v1.3 x 2
bed_mount_plate_Camellia_mod_with_cuts
RJM_01_08_1_imported x 4
belt_mount_camellia_v1.0
wiper_mount_v1.0
213x200_boro
bed_leveling_washer x 4
92161A022
92125A133 x 4
93295A032 x 4
SS_3GPT_BASE
SS_3GPT_ACTUATOR
94180A331 x 13
92095A181 x 2
93475A210 x 15
92148A150 x 15
88085K311
heated.bed.pcb.v2
92095A182 x 11
92095A183 x 2
92871A035 x 4

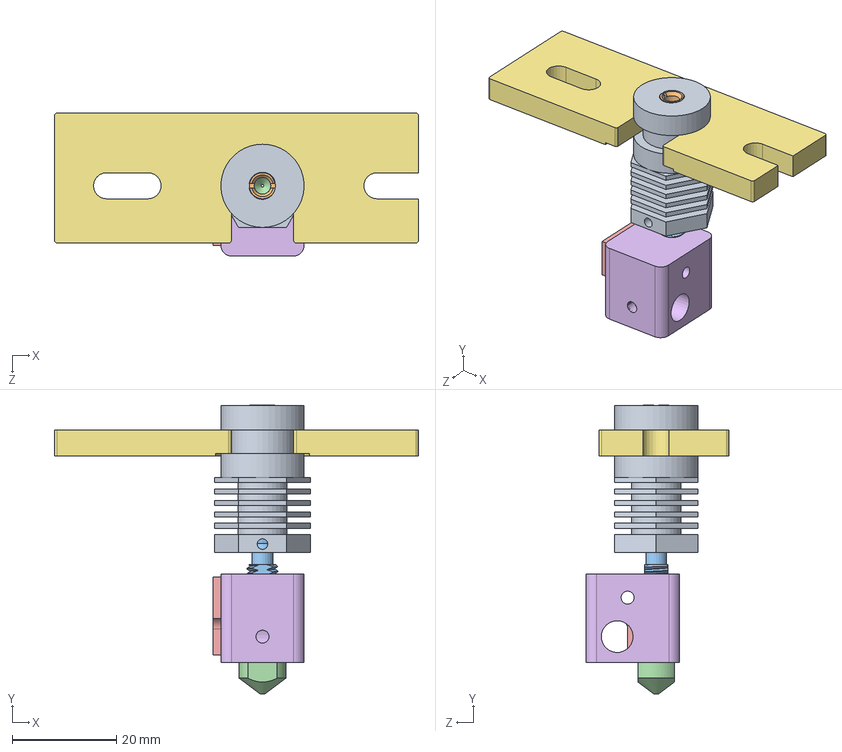
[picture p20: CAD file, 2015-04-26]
cad/solidworks/hex.nozzle/hex_nozzle.SLDASM
70.0 x 55.5 x 27.5 mm
cooling_block
upper_plug
tube_ASM
hex_nozzle
retention_plate
heating_block
hex_mount_plate

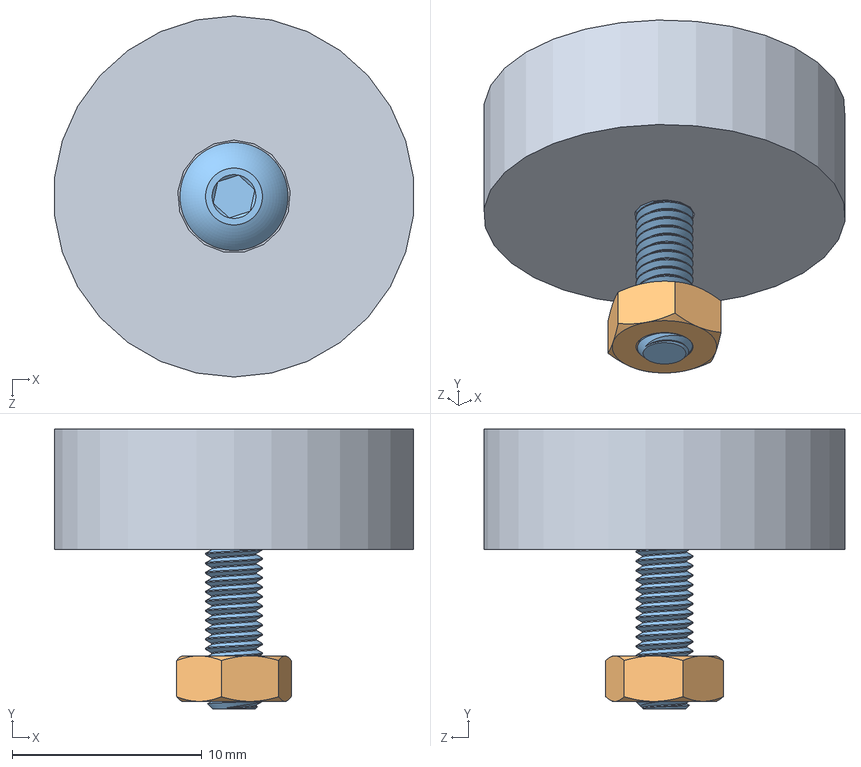
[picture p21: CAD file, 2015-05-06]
cad/solidworks/hardware/Super.Mini.Feet.Assembly.sldasm
18.9 x 14.8 x 19.1 mm
8884T13
91828A211
92095A182

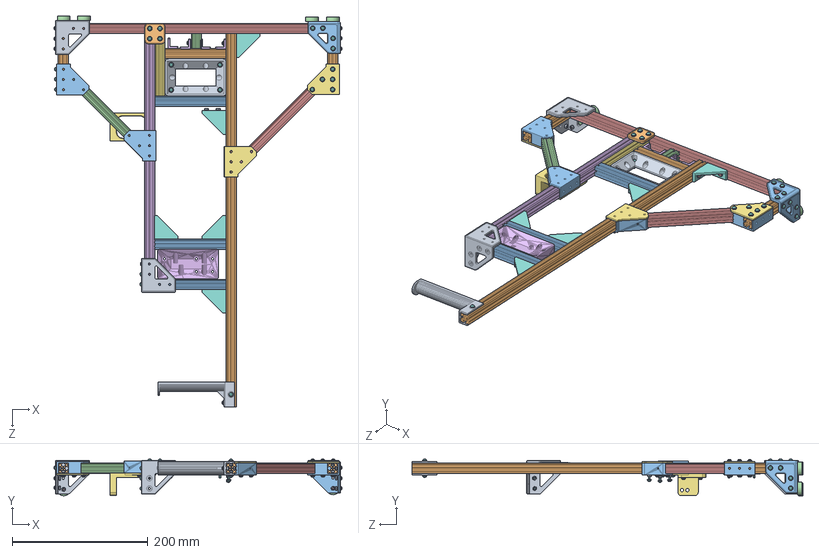
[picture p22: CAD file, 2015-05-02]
cad/solidworks/Super.Mini.Left.Frame.sldasm
424.0 x 54.0 x 576.0 mm
3-way-90deg-corner0_sldworks x 2
open.beam.extrusion.90mm x 3
open.beam.extrusion.105mm x 3
open.beam.extrusion.22mm
open.beam.extrusion.382mm
open.beam.extrusion.362mm
open.beam.extrusion.92mm
Openbeam.90.deg.strong.corner.brace x 5
kossell.spool
open.beam.extrusion.550mm
openbeam.45.deg.coupler x 4
open.beam.extrusion.143mm
open.beam.extrusion.175mm
Openbeam.inner.L.bracket.small x 4
brace_support_cover_sld x 3
92095A181 x 69
91828A211 x 80
93475A210 x 59
92148A150 x 80
8884T13 x 4
92095A182 x 8
upper.z.axis.plate3
gusset.cover.plate.and.relief.mount
92095A183 x 7
lower.z.adapter.plate.v2
OpenBeam.QuadPlate
Open.Beam.3-way.Corner

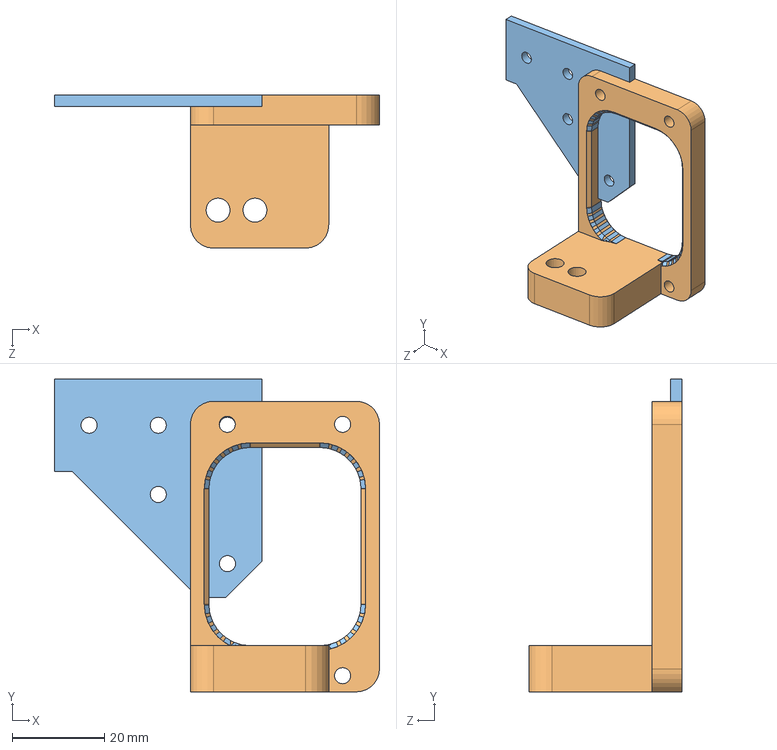
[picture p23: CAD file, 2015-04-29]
cad/solidworks/brace.support.cover.and.reliefmount.for.z.axis.SLDASM
70.5 x 67.8 x 33.3 mm

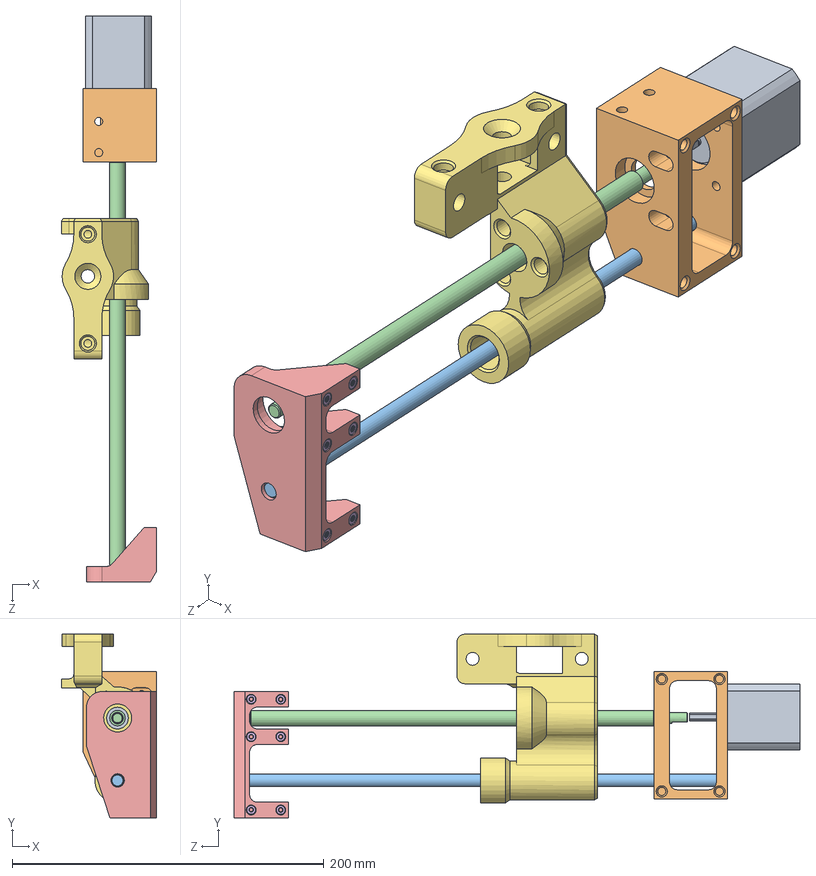
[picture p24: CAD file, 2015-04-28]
cad/solidworks/Right.Z.Assembly.sldasm
61.1 x 117.7 x 362.9 mm
NEMA-17_StepperMotor
lower_z_right_camellia_v1.1
ssfj8_315_2_03_sw
mtstrw10_287_f22_v7_s7_q7_fv0_fw10_fy1_sld3
upper_z_right_camellia_v1.2
94180A331 x 6
x_end_idler_camellia_v2.4

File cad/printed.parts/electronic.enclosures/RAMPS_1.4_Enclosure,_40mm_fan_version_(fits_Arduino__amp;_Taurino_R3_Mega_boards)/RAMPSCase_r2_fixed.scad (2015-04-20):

//
// RAMPS Case
//


// Modified by Cpayne3d December 2014
// - adjusted for 40mm x 10mm cooling fan (like ones found at www.voxelfactory.com
// - reduced fan base height to allow fan to be spaced farther away from Ramps PCB
// - increased venting holes in width and height to allow more air flow and to open up for 40mm fan
// - increased holes sizes in USB end (usb/dc power/ramps power) to properly fit the Taurino.cc version of Mega R3 + Ramp 1.4 board.  The Taurino version also has a diode on the right side which hit the inner rails.
// - added a port hole in the wiring end to allow for Reprapdiscount LCD cables to connect into the case
// - added compile option "6" to generate mounting brackets for mounting the case to a printer eg: OrdBot or i3
// - main case body unchanged from its original design
// - Do not modify parameters unless you understand the changes. Make a backup copy of this file!


// parameters
$fn=20;
c=false;  // center True/False
th=2.0;    // rib marks on outside of case
fanh=10.0;     // miniature fan height
//length=105.0;
length=105 + fanh; // add fan height
width=65.0;
height=46.0;
fh=2.0;     // feet height
mrlh=2.0;   // Left PCB mount ridge height
mrh=2.0;    // Right PCB mount ridge height
rmh=2.0;    // PCB Rail height   
rth=th+1;   // ridge thickness
mrw=3.0;    // width
mrd=2.0;    // offset
soh=6.0;    // standoff height
ch=5.0;     // cover height
cd=5.0;     // steppercable diameter

i=3; // 1=cover1, 2=cover2, 3=case, 5= case+bracket, 6=mounting bracket

if (i==1)        { Cover1();
} else if (i==2) { Cover2();
} else if (i==3) { CaseBody();
} else if (i==4) { Test();
} else if (i==5) { bracket_test();
} else if (i==6) { hadron_bracket();
}

module Test() {
   Cover2();
   translate([0,0,8])
   CaseBody();
   translate([0,0,130])
   rotate([360,180,0])
   Cover1();
}


module bracket_test() {
  translate([0,0,8])
 // CaseBody();
rampsCaseshellonly();
   //translate([0,0,2])
   hadron_bracket();
}


module hadron_bracket() {
translate([0, 0, 2])
difference() {
  union() {
   minkowski() { cube([width + 12 , height + 12, 4], center=true); cylinder(h=5, r=4, $fn=25); } // bracket ring


  // clamp connector part 1
  translate([(height/2)+17, -8, -2]) color("Blue", 1.0) cube([11, 3, 9]);

  // clamp connector part 2
  translate([(height/2)+17, -13, -2]) color("Blue", 1.0) cube([11, 3, 9]);
 

  // big foot mount point
  translate([0, height-15.5, 13]) 
  union() {
     rotate([0, 90, 0]) rotate([0, 90, 90]) minkowski() { cube([30 , 15, 3], center=true); cylinder(h=1, r=4, $fn=25); }  // bracket big foot
   } // end union for foot
   }

  union() {
   // translate([0,0, -15]) rampsCaseshellonly();
   minkowski() { cube([width-1 , height-1 , 15], center=true); cylinder(h=1, r=4, $fn=25); } // inner core removal

	//feet
	translate( [-width/2+5,25.5, -5] )
    cube( size=[5+2,fh+1,length], center=c);
	translate( [width/2-12,25.5, -5] )
    cube( size=[5+2,fh+1,length], center=c);

  // embellishments cutout
   translate( [(-height/2 )+4, -width/2+5, -5] )
     cube([15.5, 3, 15]);

  // cut to tighten clamp
  translate([(height/2)+12, -10, -3]) cube([10, 2, 15]);

 // clamp screw hole
  translate([(height/2)+24, 0, 2]) rotate([90, 0, 0]) cylinder(h=15, r=2, $fn=20);
 
   }

 } // end difference

}  // end module


module rampsCaseshellonly() {
	//case
   roundedDuct([67,48,length], 4);

	//feet
	translate( [-width/2+6,25.5,0] )
    cube( size=[5,fh,length], center=c);
	translate( [width/2-11,25.5,0] )
    cube( size=[5,fh,length], center=c);

	//embellishment
	for ( z = [0:1:5] ) {
		translate( [-5-z*1.25*th,-height/2-1.5*th,0] ) cylinder( r=th/2, h=length, center=c);
	}

}


module Cover1() {
   difference() {
 	  union() {
	    rampsCover();
	    translate([-9,0,th]) //Fan standoff
       fanmount();
	  }


      //Cableroom row2 (stepper/min/max/heater/hbp)
 	  translate( [20.5,-13,0] )
       rounded_slit(cd,2.5*cd,2*th);
	  
	  //Cableroom (reprapdiscount lcd wires)
      translate( [20,-4,0] )
       cube([cd *2, 4*cd, 2*th]); 
         //rounded_slit(cd*2.6,cd,2*th);

	  //Ventilation slits
	  for ( y = [-4.5:3.5:30] ) {
		   translate( [-10,12-y,0] )
         rounded_slit(1.5,35,2*th);
	  }
	}
}


module Cover2() {
   difference() {
	  mirror() rampsCover();
	  //USB (12x11)
	  translate( [-13.5,10.75,0] )
     cube( size=[13,11.5,2*th], center=true );
	  //Powerjack (9x11)
	  translate( [16,10.25,0] )
     cube( size=[10,11.5,2*th], center=true );
	  //Powerconnector (21x9)
	  translate( [18,-2,0] )
     cube( size=[22,10,30], center=true );
     //Connector tabs
     translate( [13,-7,0] )
     cube( size=[2.5,4,30], center=true );
     translate( [24,-7,0] )
     cube( size=[2.5,4,30], center=true );
     // Ramps PCB Edge Clearance
     translate( [27.5,2.5,5] )
     cube( size=[10,4,5], center=true );
     translate( [-27.5,2.5,5] )
     cube( size=[10,4,5], center=true );
	  //Ventilation slits
	  for ( y = [0:3.5:20] ) {
			translate( [-15,-18+y,0] ) rounded_slit(1.5,24,2*th);
	  }
  }
}

module CaseBody() {
   difference() {
     union() {
	  rampsCase();
     }
   //Reset Button Access Hole
   translate( [32.5, -2,  33])
   rotate ([0,90,0])
   cylinder( h=4,d1=4,d2=4,center=c);
   };
}

module rampsCase() {
	//case
   roundedDuct([67,48,length], 4);
	//PCB mount ridge left
	
     // original version
//	  translate( [23, 18, 9] )
//       cube( size=[9.5,3,length -18], center=c);
    // fixed version
	translate( [23, 18, 9] )
      color("red") cube( size=[10.5,3,length -18], center=c);
 
     // original version
//   translate( [23,12.5,9] )
//      cube( size=[9.5,3,length -18], center=c);
   // fixed version
   translate( [23,12.5,9] )
      color("red") cube( size=[10.5,3,length -18], center=c);

     // original version
//    translate( [26,15.5,9] )
//      cube( size=[7,3,length -18], center=c);
    // fixed version
    translate( [26,15.5,9] )
      color("red") cube( size=[8,3,length -18], center=c);


     // original version
	// right
//	translate( [-32.5,18,9] ) 
//      cube( size=[4.5,3,length-18], center=c);
	// right - fixed version
	translate( [-34.5,18,9] ) 
      color("red") cube( size=[6.5,3,length-18], center=c);

     // original version
	//upper right (shortened to leave room for the reset switch)
//	translate( [-32.5,12.5,9] )
//      cube( size=[4.5,3,length-18], center=c);
    // upper right - fixed version
	translate( [-34.5,12.5,9] )
      color("red") cube( size=[6.5,3,length-18], center=c);

// Test for Mounting Cone placment
//    translate( [23, 20, 0] )
//    cube( size=[4.5,3,8], center=c);
// Test for Mounting Cone placment

	//feet
	translate( [-width/2+6,25.5,0] )
    cube( size=[5,fh,length], center=c);
	translate( [width/2-11,25.5,0] )
    cube( size=[5,fh,length], center=c);

	//embellishment
	for ( z = [0:1:5] ) {
		translate( [-5-z*1.25*th,-height/2-1.5*th,0] ) cylinder( r=th/2, h=length, center=c);
	}

	//bottom cover mount
	translate( [-width/2,height/2,12]  ) rotate(v=[1,1,0], a=180) rotate( v=[0,0,1], a=45 ) mountCone();
	translate( [-width/2,-height/2,12]  ) rotate(v=[1,1,0], a=180) rotate( v=[0,0,1], a=-45 ) mountCone();
	translate( [width/2,-height/2,12]  ) rotate(v=[1,1,0], a=180) rotate( v=[0,0,1], a=-135 ) mountCone();
	translate( [width/2,height/2,12]  ) rotate(v=[1,1,0], a=180) rotate( v=[0,0,1], a=135 ) mountCone();

	//top cover mount
	translate( [width/2,-height/2,length-12]  ) rotate( v=[0,0,1], a=45 ) mountCone();
	translate( [-width/2,-height/2,length-12]  ) rotate( v=[0,0,1], a=-45 ) mountCone();
	translate( [-width/2,height/2,length-12]  ) rotate( v=[0,0,1], a=-135 ) mountCone();
	translate( [width/2,height/2,length-12]  ) rotate( v=[0,0,1], a=135 ) mountCone();
}

module rampsCover() {

   roundedDuct([67,48,ch], 4);
   translate( [0,0,0] )
   roundedRect([67,48,th], 4);

// original
	//ridge
	//translate( [0,(height-rth+.7)/2,ch] ) cube( size=[width-14,rth,ch], center=true );
// fixed version
	translate( [0,(height-rth+.7)/2,ch-1] ) color("red") cube( size=[width-14,rth,ch+1.75], center=true );

// original
	//translate( [0,-(height-rth-1.3)/2,ch] ) cube( size=[width-14,rth,ch], center=true );
// fixed version
	translate( [0,-(height-rth-1.3)/2,ch-1] ) color("red") cube( size=[width-14,rth,ch+1.75], center=true );

// original
	//translate( [((width-rth)/2)-.3,0,ch] ) cube( size=[rth,height-14,ch], center=true );
// fixed version
	translate( [((width-rth)/2)-.3,0,ch-1] ) color("red") cube( size=[rth,height-14,ch+1.75], center=true );

// original
	//translate( [-((width-rth)/2)+.3,0,ch] ) cube( size=[rth,height-14,ch], center=true );

// fixed version
	translate( [-((width-rth)/2)+.3,0,ch-1] ) color("green") cube( size=[rth,height-14,ch+1.75], center=true );


	//embellishment
	for ( z = [0:1:5] ) {
		translate( [5+z*1.25*th,-height/2-1.5*th,0] ) 
        cylinder( r=th/2, h=ch, center=c);
	}
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

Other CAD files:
cad/solidworks/vendor.models/HSK1_ASM_ASM.sldasm
cad/solidworks/vendor.models/T44-ES1107A302-20130510_ASM.sldasm
cad/solidworks/Extruder.and.Mount.Assembly.sldasm
cad/solidworks/vendor.models/ASSEM1_ASM.sldasm
cad/COTS/lulzbot_edition_hexagon_hotend-3mm/HB 16x18x17 v4.DXF
cad/COTS/lulzbot_edition_hexagon_hotend-3mm/HB 16x18x17 v4.SLDDRW
cad/COTS/lulzbot_edition_hexagon_hotend-3mm/cooling block 3mm short .DXF
cad/COTS/lulzbot_edition_hexagon_hotend-3mm/cooling block 3mm short .SLDDRW
cad/COTS/lulzbot_edition_hexagon_hotend-3mm/nozle v3 3.2 0.4.DXF
cad/COTS/lulzbot_edition_hexagon_hotend-3mm/nozle v3 3.2 0.4.SLDDRW
cad/COTS/lulzbot_edition_hexagon_hotend-3mm/retention plate V2 .DXF
cad/COTS/lulzbot_edition_hexagon_hotend-3mm/retention plate V2 .SLDDRW
cad/COTS/lulzbot_edition_hexagon_hotend-3mm/tube ASM long HB.DXF
cad/COTS/lulzbot_edition_hexagon_hotend-3mm/tube ASM long HB.SLDDRW
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

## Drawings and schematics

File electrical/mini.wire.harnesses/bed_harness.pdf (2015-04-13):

## Harness General Assembly Instruction:

## 1. Crimp Rambo end FIRST

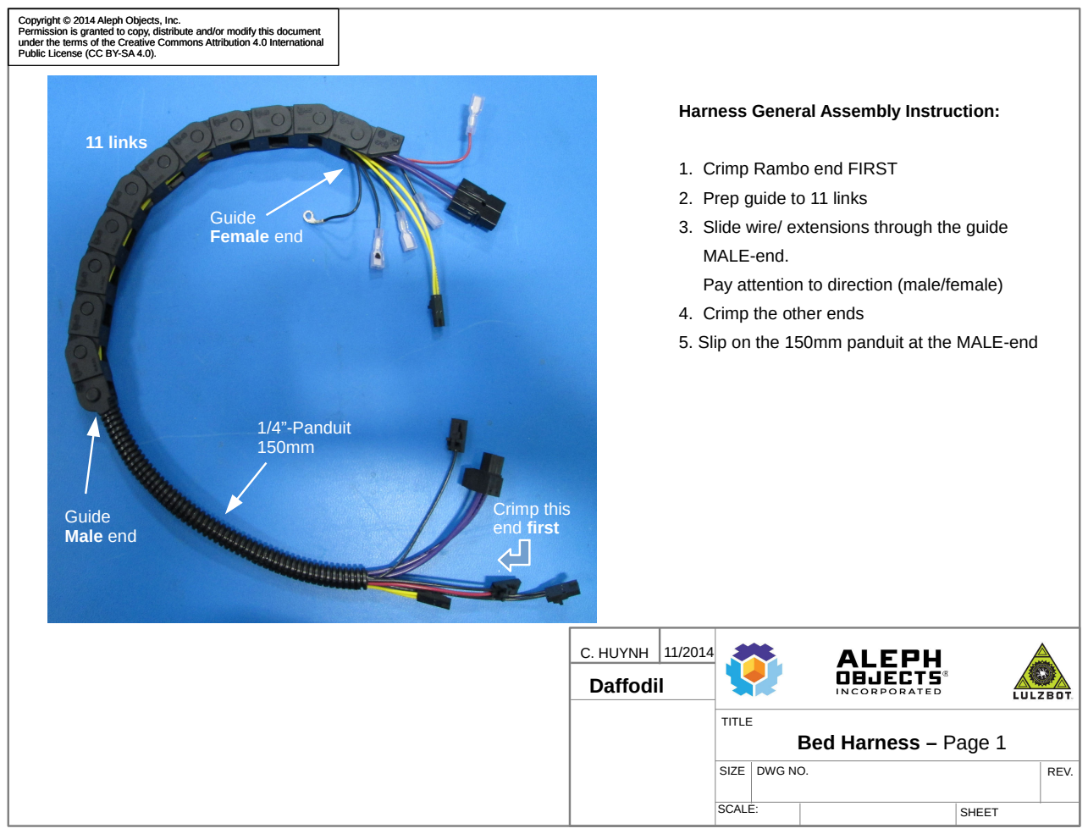
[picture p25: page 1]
C. HUYNH; TITLE; Daffodil; Crimp this; 11 links; Guide Female end; 1/4”-Panduit 150mm

Copyright © 2014 Aleph Objects, Inc.
Permission is granted to copy, distribute and/or modify this document
under the terms of the Creative Commons Attribution 4.0 International
Public License (CC BY-SA 4.0).

2. Prep guide to 11 links
3. Slide wire/ extensions through the guide
MALE-end.
Pay attention to direction (male/female)
4. Crimp the other ends
5. Slip on the 150mm panduit at the MALE-end

end first Guide
Male end

Bed Harness – Page 1

SIZE | DWG NO. | REV.

SCALE: | | SHEET

## 16AWG Purple, L= 550mm (pre-stripped)

## [EL-WR0108]

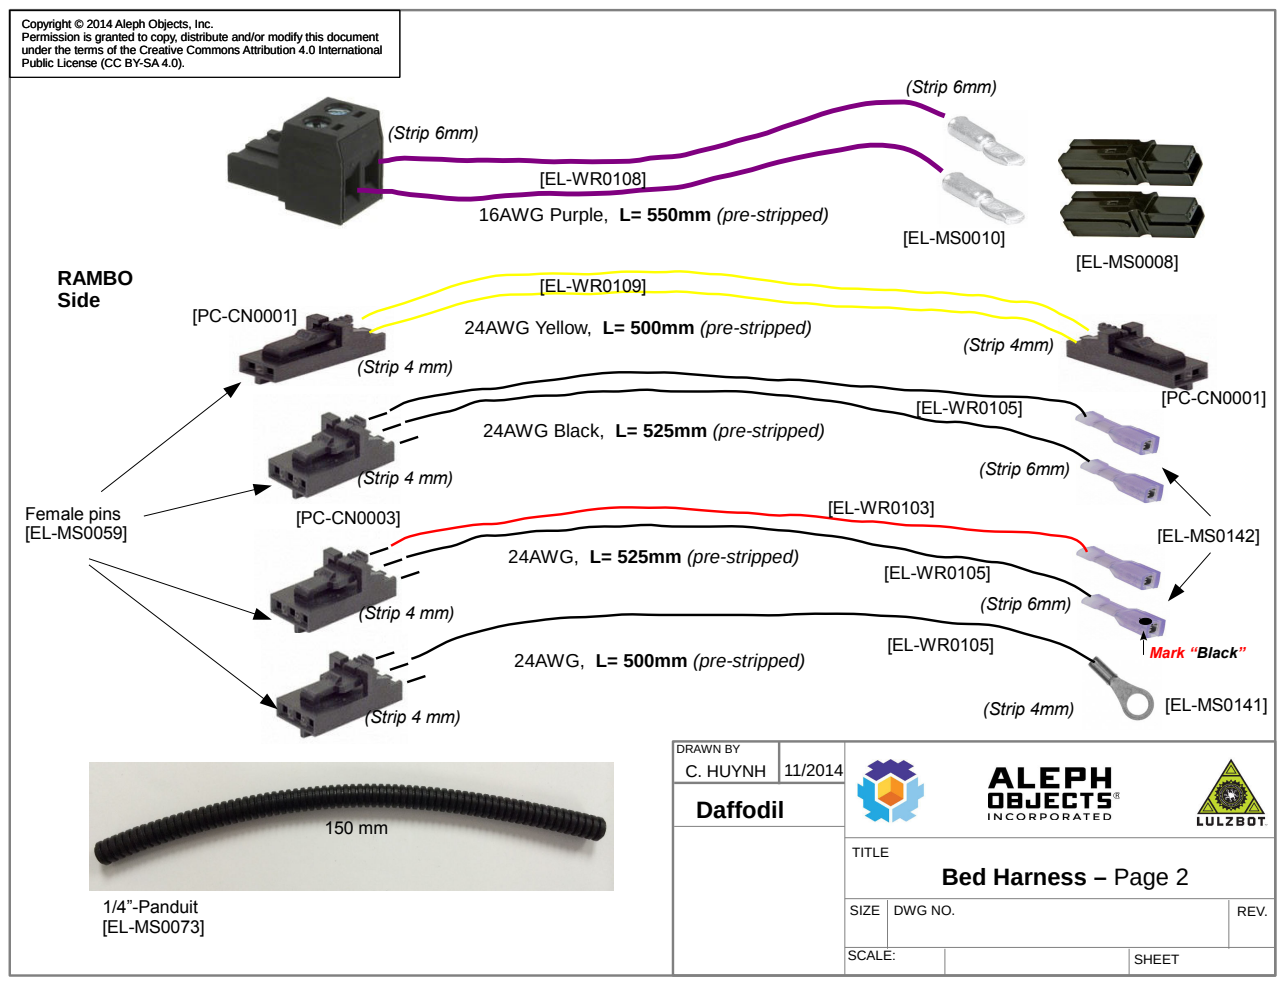
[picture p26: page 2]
DRAWN BY; C. HUYNH; TITLE; RAMBO Side; (Strip 6mm); (Strip 4mm); (Strip 4 mm); Female pins; 24AWG, L= 525mm (pre-stripped); 24AWG, L= 500mm (pre-stripped); Daffodil; Mark “Black”; 1/4”-Panduit [EL-MS0073]

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

24AWG Yellow, L= 500mm (pre-stripped)

24AWG Black, L= 525mm (pre-stripped)

Bed Harness – Page 2

SIZE | DWG NO. | REV.

SCALE: | | SHEET

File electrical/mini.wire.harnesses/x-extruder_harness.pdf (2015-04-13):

## Harness General Assembly Instruction:

## 1. Prep 2 guides – 18 links & 11 links

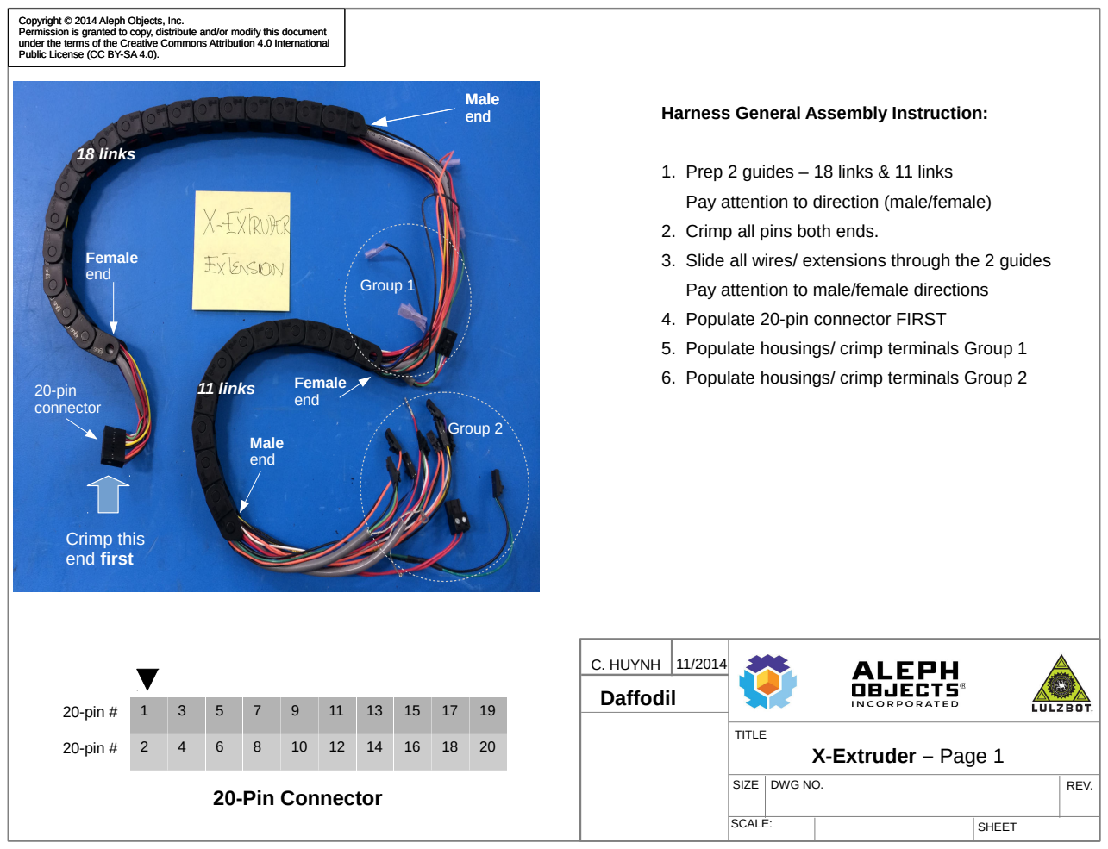
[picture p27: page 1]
C. HUYNH; TITLE; X-Extruder – Page 1; Daffodil; Crimp this end first; Male end; 11 links; 18 links; Female end; Female end 20-pin connector; Group 1; Group 2; 20-pin #; 20-Pin Connector

Copyright © 2014 Aleph Objects, Inc.
Permission is granted to copy, distribute and/or modify this document
under the terms of the Creative Commons Attribution 4.0 International
Public License (CC BY-SA 4.0).

Pay attention to direction (male/female)
2. Crimp all pins both ends.
3. Slide all wires/ extensions through the 2 guides
Pay attention to male/female directions
4. Populate 20-pin connector FIRST
5. Populate housings/ crimp terminals Group 1
6. Populate housings/ crimp terminals Group 2

SIZE | DWG NO. | REV.

SCALE: | | SHEET

## L= 1080 mm (pre-stripped)

20-pin 18 | (Strip 30mm)

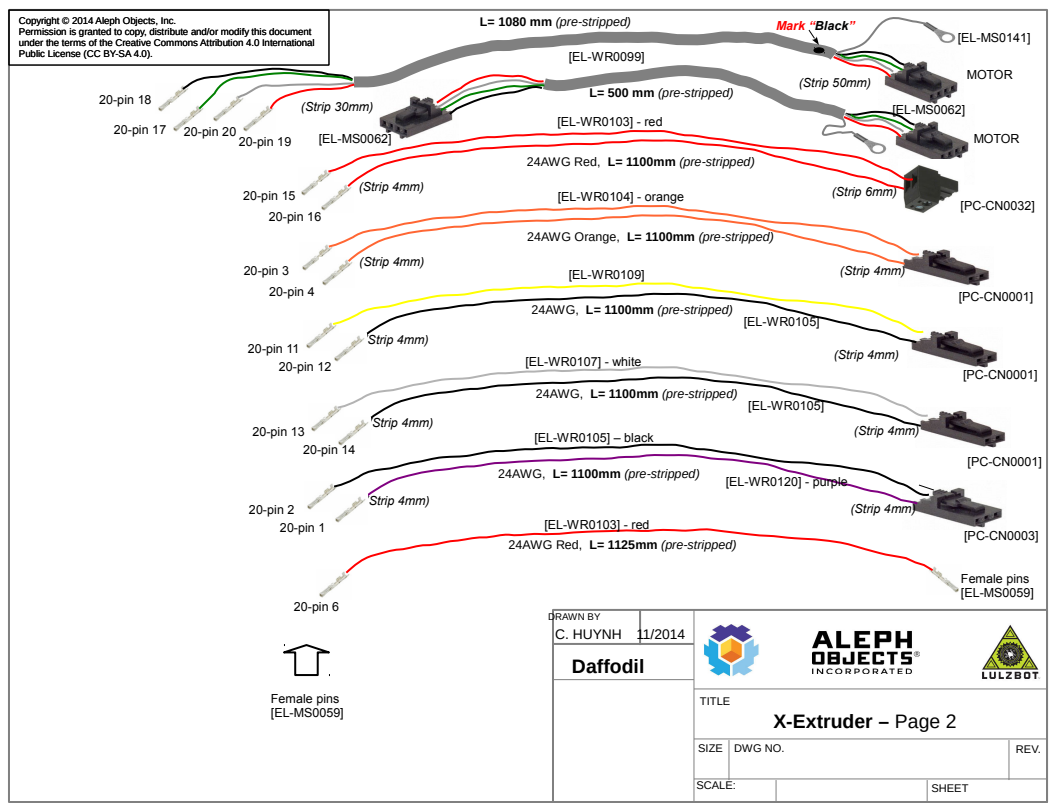
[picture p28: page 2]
DRAWN BY C. HUYNH 11/2014; TITLE; SIZE; DWG NO.; REV.; X-Extruder – Page 2; Daffodil; (Strip 50mm); 20-pin 17; 20-pin 20; 20-pin 19; [EL-WR0103] - red; (Strip 6mm) (Strip 4mm); 20-pin 15; 20-pin 16; [EL-WR0104] - orange; (Strip 4mm); 20-pin 3; 20-pin 4; 24AWG, L= 1100mm (pre-stripped); 20-pin 11; 20-pin 12; (Strip 4mm) (Strip 4mm); 20-pin 13; 20-pin 14; [EL-WR0107] - white; MOTOR; 20-pin 2; [PC-CN0003] 20-pin 1; [EL-WR0105] – black; [EL-WR0120] - purple; Female pins [EL-MS0059]; 20-pin 6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

Public License (CC BY-SA 4.0).

L= 500 mm (pre-stripped)

24AWG Red, L= 1100mm (pre-stripped)

24AWG Orange, L= 1100mm (pre-stripped)

24AWG Red, L= 1125mm (pre-stripped)

## 24AWG, L= 500mm (pre-stripped)

## (Strip 4mm)

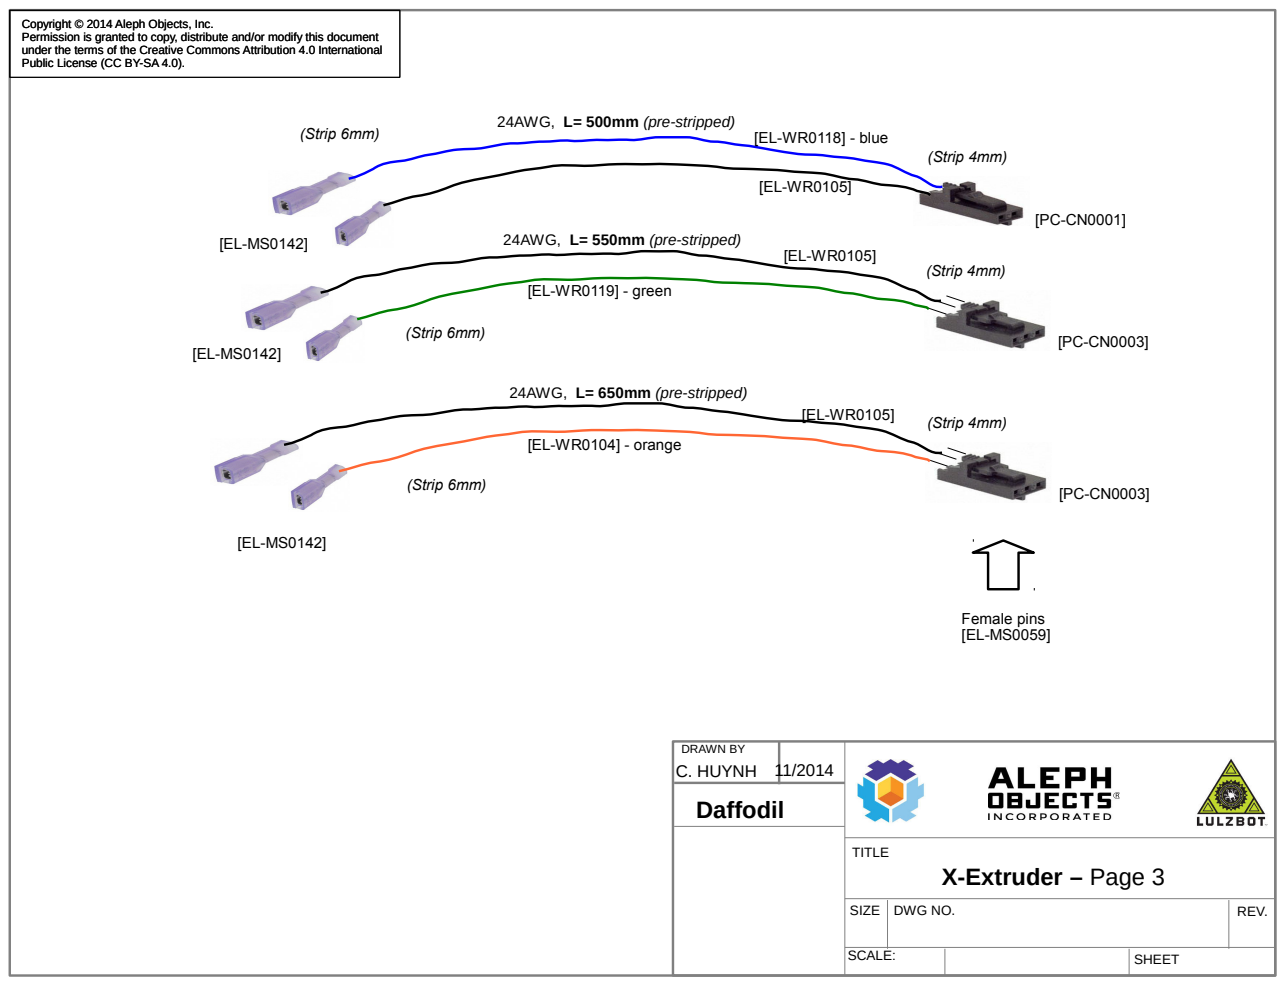
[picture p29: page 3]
DRAWN BY C. HUYNH 11/2014; TITLE; SIZE; DWG NO.; REV.; X-Extruder – Page 3; Daffodil; (Strip 6mm); [EL-WR0118] - blue; Female pins [EL-MS0059]; 24AWG, L= 550mm (pre-stripped); (Strip 4mm); [EL-WR0119] - green; 24AWG, L= 650mm (pre-stripped); [EL-WR0104] - orange

Public License (CC BY-SA 4.0).

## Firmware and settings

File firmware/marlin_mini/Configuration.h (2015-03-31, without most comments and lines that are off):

#define CONFIGURATION_H
#define STRING_VERSION_CONFIG_H __DATE__ " " __TIME__ // build date and time
#define STRING_CONFIG_H_AUTHOR "(Aleph Objects Inc, Mini-2014Q4)" // Who made the changes.
#define SERIAL_PORT 0
#define BAUDRATE 115200
#define MOTHERBOARD 302
#define EXTRUDERS 1
#define POWER_SUPPLY 1
#define TEMP_SENSOR_0 5
#define TEMP_SENSOR_1 5
#define TEMP_SENSOR_2 0
#define TEMP_SENSOR_BED 7
#define MAX_REDUNDANT_TEMP_SENSOR_DIFF 10
#define TEMP_RESIDENCY_TIME 0.5  // (seconds)
#define TEMP_HYSTERESIS 10       // (degC) range of +/- temperatures considered "close" to the target one
#define TEMP_WINDOW     10       // (degC) Window around target to start the residency timer x degC early.
#define HEATER_0_MINTEMP 5
#define HEATER_1_MINTEMP 5
#define HEATER_2_MINTEMP 5
#define BED_MINTEMP 5
#define HEATER_0_MAXTEMP 305
#define HEATER_1_MAXTEMP 305
#define HEATER_2_MAXTEMP 305
#define BED_MAXTEMP 150
#define PIDTEMP
#define BANG_MAX 220  // limits current to nozzle while in bang-bang mode; 255=full current
#define PID_MAX 225 // limits current to nozzle while PID is active (see PID_FUNCTIONAL_RANGE below); 255=full current
  #define PID_FUNCTIONAL_RANGE 16 // If the temperature difference between the target temperature and the actual temperature
  #define PID_INTEGRAL_DRIVE_MAX 220  //limit for the integral term
  #define K1 0.95 //smoothing factor within the PID
  #define PID_dT ((OVERSAMPLENR * 8.0)/(F_CPU / 64.0 / 256.0)) //sampling period of the temperature routine
    #define  DEFAULT_Kp 28.79
    #define  DEFAULT_Ki 1.91
    #define  DEFAULT_Kd 108.51
#define PIDTEMPBED
#define MAX_BED_POWER 255 // limits duty cycle to bed; 255=full current
    #define  DEFAULT_bedKp 294
    #define  DEFAULT_bedKi 65
    #define  DEFAULT_bedKd 382
#define PREVENT_DANGEROUS_EXTRUDE
#define PREVENT_LENGTHY_EXTRUDE
#define EXTRUDE_MINTEMP 120
#define EXTRUDE_MAXLENGTH (X_MAX_LENGTH+Y_MAX_LENGTH) //prevent extrusion of very large distances.
#define ENDSTOPPULLUPS // Comment this out (using // at the start of the line) to disable the endstop pullup resistors
  #define ENDSTOPPULLUP_XMAX
  #define ENDSTOPPULLUP_YMAX
  #define ENDSTOPPULLUP_ZMAX
  #define ENDSTOPPULLUP_XMIN
  #define ENDSTOPPULLUP_YMIN
  #define ENDSTOPPULLUP_ZMIN
const bool X_MIN_ENDSTOP_INVERTING = true; // set to true to invert the logic of the endstop.
const bool Y_MIN_ENDSTOP_INVERTING = true; // set to true to invert the logic of the endstop.
const bool Z_MIN_ENDSTOP_INVERTING = true; // set to true to invert the logic of the endstop.
const bool X_MAX_ENDSTOP_INVERTING = true; // set to true to invert the logic of the endstop.
const bool Y_MAX_ENDSTOP_INVERTING = true; // set to true to invert the logic of the endstop.
const bool Z_MAX_ENDSTOP_INVERTING = true; // set to true to invert the logic of the endstop.
#if defined(COREXY) && !defined(DISABLE_MAX_ENDSTOPS)
  #define DISABLE_MAX_ENDSTOPS
#endif
#define X_ENABLE_ON 0
#define Y_ENABLE_ON 0
#define Z_ENABLE_ON 0
#define E_ENABLE_ON 0 // For all extruders
#define DISABLE_X false
#define DISABLE_Y false
#define DISABLE_Z false
#define DISABLE_E false // For all extruders
#define INVERT_X_DIR false    // for Mendel set to false, for Orca set to true
#define INVERT_Y_DIR true    // for Mendel set to true, for Orca set to false
#define INVERT_Z_DIR false     // for Mendel set to false, for Orca set to true
#define INVERT_E0_DIR true   // for direct drive extruder v9 set to true, for geared extruder set to false
#define INVERT_E1_DIR true    // for direct drive extruder v9 set to true, for geared extruder set to false
#define INVERT_E2_DIR true   // for direct drive extruder v9 set to true, for geared extruder set to false
#define X_HOME_DIR -1
#define Y_HOME_DIR -1
#define Z_HOME_DIR 1
#define min_software_endstops false // If true, axis won't move to coordinates less than HOME_POS.
#define max_software_endstops true  // If true, axis won't move to coordinates greater than the defined lengths below.
#define X_MAX_POS 165
#define X_MIN_POS 0
#define Y_MAX_POS 185
#define Y_MIN_POS 0
#define Z_MAX_POS 159
#define Z_MIN_POS 0
#define X_MAX_LENGTH (X_MAX_POS - X_MIN_POS)
#define Y_MAX_LENGTH (Y_MAX_POS - Y_MIN_POS)
#define Z_MAX_LENGTH (Z_MAX_POS - Z_MIN_POS)
#define ENABLE_AUTO_BED_LEVELING // Delete the comment to enable (remove // at the start of the line)
  #define AUTO_BED_LEVELING_GRID
    #define LEFT_PROBE_BED_POSITION 0
    #define RIGHT_PROBE_BED_POSITION 160
    #define BACK_PROBE_BED_POSITION 160
    #define FRONT_PROBE_BED_POSITION 0
   #define AUTO_BED_LEVELING_GRID_POINTS 2
  #define X_PROBE_OFFSET_FROM_EXTRUDER 0
  #define Y_PROBE_OFFSET_FROM_EXTRUDER 0
  #define Z_PROBE_OFFSET_FROM_EXTRUDER -1.375
  #define Z_RAISE_BEFORE_HOMING 5       // (in mm) Raise Z before homing (G28) for Probe Clearance.
  #define XY_TRAVEL_SPEED 18000         // X and Y axis travel speed between probes, in mm/min
  #define Z_RAISE_BEFORE_PROBING 5    //How much the extruder will be raised before traveling to the first probing point.
  #define Z_RAISE_BETWEEN_PROBINGS 5  //How much the extruder will be raised when traveling from between next probing points
  #define Z_SAFE_HOMING   // This feature is meant to avoid Z homing with probe outside the bed area.
    #define Z_SAFE_HOMING_X_POINT (X_MAX_LENGTH/200)    // X point for Z homing when homing all axis (G28)
    #define Z_SAFE_HOMING_Y_POINT (Y_MAX_LENGTH/90)    // Y point for Z homing when homing all axis (G28)
#define MANUAL_X_HOME_POS 0
#define MANUAL_Y_HOME_POS 0
#define MANUAL_Z_HOME_POS 0
#define NUM_AXIS 4 // The axis order in all axis related arrays is X, Y, Z, E
#define HOMING_FEEDRATE {30*60, 30*60, 12*60, 0}  // set the homing speeds (mm/min)
#define DEFAULT_AXIS_STEPS_PER_UNIT   {100.5,100.5,1600,833}  // default steps per unit for Ultimaker
#define DEFAULT_MAX_FEEDRATE          {800, 800, 8, 40}    // (mm/sec)
#define DEFAULT_MAX_ACCELERATION      {9000,9000,100,1000}    // X, Y, Z, E maximum start speed for accelerated moves. E default values are good for Skeinforge 40+, for older versions raise them a lot.
#define DEFAULT_ACCELERATION          2000    // X, Y, Z and E max acceleration in mm/s^2 for printing moves
#define DEFAULT_RETRACT_ACCELERATION  3000   // X, Y, Z and E max acceleration in mm/s^2 for retracts
#define DEFAULT_XYJERK                12.0    // (mm/sec)
#define DEFAULT_ZJERK                 0.4     // (mm/sec)
#define DEFAULT_EJERK                10.0    // (mm/sec)
#define CUSTOM_M_CODES
  #define CUSTOM_M_CODE_SET_Z_PROBE_OFFSET 851
  #define Z_PROBE_OFFSET_RANGE_MIN -15
  #define Z_PROBE_OFFSET_RANGE_MAX 5
#define EEPROM_SETTINGS
#define EEPROM_CHITCHAT
#define PLA_PREHEAT_HOTEND_TEMP 180
#define PLA_PREHEAT_HPB_TEMP 70
#define PLA_PREHEAT_FAN_SPEED 255   // Insert Value between 0 and 255
#define ABS_PREHEAT_HOTEND_TEMP 240
#define ABS_PREHEAT_HPB_TEMP 100
#define ABS_PREHEAT_FAN_SPEED 255   // Insert Value between 0 and 255
#define FAST_PWM_FAN
#define NUM_SERVOS 1 // Servo index starts with 0 for M280 command
#define SERVO_ENDSTOPS {-1, -1, 0} // Servo index for X, Y, Z. Disable with -1
#define SERVO_ENDSTOP_ANGLES {0,0, 0,0, 70,0} // X,Y,Z Axis Extend and Retract angles
#include "Configuration_adv.h"
#include "thermistortables.h"

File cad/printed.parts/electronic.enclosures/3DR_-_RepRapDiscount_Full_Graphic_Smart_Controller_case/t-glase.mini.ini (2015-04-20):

[profile]
layer_height = .5
wall_thickness = 1.2
retraction_enable = True
solid_layer_thickness = 1.2
fill_density = 30
nozzle_size = .6
print_speed = 14
print_temperature = 240
print_temperature2 = 0
print_temperature3 = 0
print_temperature4 = 0
print_bed_temperature = 60
support = None
platform_adhesion = None
support_dual_extrusion = Second extruder
wipe_tower = True
wipe_tower_volume = 15
ooze_shield = False
filament_diameter = 2.89
filament_diameter2 = 2.89
filament_diameter3 = 0
filament_diameter4 = 0
filament_flow = 100.0
retraction_speed = 10
retraction_amount = 1
retraction_dual_amount = 25
retraction_min_travel = 1.5
retraction_combing = True
retraction_minimal_extrusion = 0.02
retraction_hop = 0
bottom_thickness = .5
layer0_width_factor = 200
object_sink = 0
overlap_dual = 0
travel_speed = 100
bottom_layer_speed = 10
infill_speed = 14
inset0_speed = 14
insetx_speed = 14
cool_min_layer_time = 45
fan_enabled = True
skirt_line_count = 2
skirt_gap = 6
skirt_minimal_length = 0
fan_full_height = .5
fan_speed = 40
fan_speed_max = 50
cool_min_feedrate = 7
cool_head_lift = False
solid_top = True
solid_bottom = True
fill_overlap = 10
support_type = Grid
support_angle = 45
support_fill_rate = 30
support_xy_distance = 0
support_z_distance = 0
spiralize = False
simple_mode = False
brim_line_count = 2
raft_margin = 3
raft_line_spacing = 1.0
raft_base_thickness = .5
raft_base_linewidth = 0.7
raft_interface_thickness = 0.2
raft_interface_linewidth = 0.2
raft_airgap = 0.22
raft_surface_layers = 2
fix_horrible_union_all_type_a = False
fix_horrible_union_all_type_b = False
fix_horrible_use_open_bits = False
fix_horrible_extensive_stitching = False
plugin_config = (lp1
	.
object_center_x = -1
object_center_y = -1

[alterations]
start.gcode = ;This Gcode has been generated specifically for the LulzBot Mini
	;Basic settings: Layer height: {layer_height} Walls: {wall_thickness} Fill: {fill_density}
	;Filament Diameter: {filament_diameter}
	;Nozzle Size: {nozzle_size}
	G21                          ; metric values
	G90                          ; absolute positioning
	M82                          ; set extruder to absolute mode
	M107                         ; start with the fan off
	G92 E0                       ; set extruder position to 0
	M140 S{print_bed_temperature}; get bed heating up
	G28                          ; home all
	M109 S140                    ; set to cleaning temp and wait
	G1 Z150 E-30 F75             ; suck up XXmm of filament
	M109 S160                    ; heat up rest of way
	G1 X45 Y174 F11520           ; move behind scraper
	G1 Z0  F1200                 ; CRITICAL: set Z to height of top of scraper
	G1 X45 Y174 Z-.5 F4000       ; wiping ; plunge into wipe pad
	G1 X55 Y172 Z-.5 F4000       ; wiping
	G1 X45 Y174 Z0 F4000         ; wiping
	G1 X55 Y172 F4000            ; wiping
	G1 X45 Y174 F4000            ; wiping
	G1 X55 Y172 F4000            ; wiping
	G1 X45 Y174 F4000            ; wiping
	G1 X55 Y172 F4000            ; wiping
	G1 X60 Y174 F4000            ; wiping
	G1 X80 Y172 F4000            ; wiping
	G1 X60 Y174 F4000            ; wiping
	G1 X80 Y172 F4000            ; wiping
	G1 X60 Y174 F4000            ; wiping
	G1 X90 Y172 F4000            ; wiping
	G1 X80 Y174 F4000            ; wiping
	G1 X100 Y172 F4000           ; wiping
	G1 X80 Y174 F4000            ; wiping
	G1 X100 Y172 F4000           ; wiping
	G1 X80 Y174 F4000            ; wiping
	G1 X100 Y172 F4000           ; wiping
	G1 X110 Y174 F4000           ; wiping
	G1 X100 Y172 F4000           ; wiping
	G1 X110 Y174 F4000           ; wiping
	G1 X100 Y172 F4000           ; wiping
	G1 X110 Y174 F4000           ; wiping
	G1 X115 Y172 Z-0.5 F1000     ; wipe slower and bury noz in cleanish area
	G1 Z10                       ; raise z
	G28 X0 Y0                    ; home x and y
	M109 S160                    ; set to probing temp
	M204 S300                    ; Set probing acceleration
	G29                          ; Probe
	M204 S2000                   ; Restore standard acceleration
	G1 X5 Y15 Z10 F5000          ; get out the way
	G4 S1                        ; pause
	M400                         ; clear buffer
	M109 S{print_temperature}    ; set extruder temp and wait
	G4 S15                       ; wait for bed to temp up
	G1 Z2 E0 F75                 ; extrude filament back into nozzle
	M140 S{print_bed_temperature}; get bed temping up during first layer
end.gcode = M400
	M104 S0                                      ; hotend off
	M140 S0                                      ; heated bed heater off (if you have it)
	M107                                         ; fans off
	G92 E5                                       ; set extruder to 5mm for retract on print end
	G1 X5 Y5 Z156 E0 F10000                      ; move to cooling positioning
	M190 R50                                     ; wait for bed to cool
	M104 S0                                      ;
	G1 X145 Y175 Z156 F1000                      ; move to cooling positioning
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

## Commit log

2015-03-31 Start of github master
    [Configuration.h, Configuration_adv.h, HB 16x18x17 v4.DXF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]
2015-03-31 Added solidworks models
    [94180A307.SLDPRT, 94180A331.SLDPRT, 94180A361.SLDPRT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]
2015-04-01 Bom refactoring
    [supermini_bom.xlsx]
2015-04-01 Model updating
    [14RTopVert.SLDPRT, 14RTopVert.stl, OBCnr4.stl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]
2015-04-02 Bom, added new part
    [lower_z_left_camellia_v1.1.STL, supermini_bom.xlsx, upper_z_left_v1.2_Mini.STL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]
2015-04-07 More parts
    [mini.bed.plate.for.200mm.dxf, supermini_bom.xlsx]
2015-04-08 Model Work
    [14RTopVert.SLDPRT, 213x200_boro.SLDPRT, ArmBracket.stl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]
2015-04-09 added wiper mount, bom update
    [supermini_bom.xlsx, wiper_mount_v1.0.fcstd, wiper_mount_v1.0.stl]
2015-04-09 Bed Work
    [94125K422.SLDPRT, 94125K422_compressed.SLDPRT, 9434K113.SLDPRT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]
2015-04-09 Bed Hardware
    [91116A120.SLDPRT, 92125A133.SLDPRT, 92161A022.SLDPRT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]
2015-04-13 Bom works and new models
    [3-way-90deg-corner0_repaired.stl, CableChain.stl, CableChainEnds.stl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]
2015-04-14 Assembly model work
    [Open.beam.small.L.bracket.SLDPRT, Openbeam.inner.L.bracket.small.SLDPRT, Openbeam_90_degree_inner_bracket.stl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]
2015-04-14 Frame model work
    [brace_support_cover.stl, brace_support_cover_sld.SLDPRT, open.beam.extrusion.405mm.SLDPRT]
2015-04-16 Model Spool and hardware
    [91828A211.SLDPRT, 92095A181.SLDPRT, 92148A150.SLDPRT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]
2015-04-20 LCD model & hardware
    [92095A168.SLDPRT, 92095A182.SLDPRT, 92095A183.SLDPRT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]
2015-04-21 SW2014 rollback and work hardware models
    [8884T13.SLDPRT, 92095A183.SLDPRT, LCD.Assembly.SLDASM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]
2015-04-24 Directory Cleanup, model work.
    [91116A120.SLDPRT, 92125A133.SLDPRT, 92161A022.SLDPRT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]
2015-04-24 Directory cleanup
    [91116A120.SLDPRT, 92125A133.SLDPRT, 92161A022.SLDPRT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]
2015-04-24 Model hardware
    [92015A104.SLDPRT, 94180A307.SLDPRT, 94180A361.SLDPRT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]
2015-04-26 Lots of model work
    [3-way-90deg-corner0_no.cube.SLDPRT, 40mm_Fan.SLDPRT, 92095A211.SLDPRT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]
2015-04-27 More Model work
    [CableChain.SLDPRT, M3.10mm.Screw.Combo.SLDASM, M3.6mm.Screw.Combo.SLDASM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]
2015-04-27 STL for drag chain mount
    [brace.support.cover.and.reliefmount.for.z.axis.v1.STL]
2015-04-27 Model mating work
    [Extruder.and.Mount.Assembly.sldasm, Left.Z.Assembly.sldasm, Lulzbot.Mini.COTS.Extruder.SLDASM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]
2015-04-27 Model mating
    [HeatSet.M3.Insert.Setscrew.Combo.sldasm, LCD.Assembly.SLDASM, Left.Z.Assembly.sldasm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]
2015-04-30 New Lower Z adapter plate.
    [adapter.plate.test.assem.SLDASM, lower.z.adapter.plate.v2.SLDPRT, lower.z.adapter.plate.v2.STL]
2015-05-01 Model rework
    [Open.Beam.3-way.Corner.SLDPRT, OpenBeam.QuadPlate.SLDPRT, OpenBeam.QuadPlate.STL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]
2015-05-01 Updated filament diameter
2015-05-04 Major Model rework
    [HeatSet.M3.Insert.Setscrew.Combo.sldasm, M3.10mm.Screw.Combo.SLDASM, M3.12mm.Screw.Combo.SLDASM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]
2015-05-04 Spool Holder
    [Open.Beam.Spool.Holder.SLDPRT]
2015-05-06 Bed Assembly work
    [Bed.Assembly.sldasm, bed_mount_plate_Camellia_mod_with_cuts.SLDPRT, heated.bed.pcb.v2.SLDPRT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]
2015-05-11 More models
    [HeatSet.M3.Insert.Setscrew.Combo.sldasm, M3.10mm.Screw.Combo.SLDASM, M3.12mm.Screw.Combo.SLDASM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]
2015-05-14 Starting new concept with MDF panels
    [90576A104.SLDPRT, 91166A240.SLDPRT, 92461A200.SLDPRT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]
2015-05-14 Flange design
    [upper_z_left_flanged.SLDPRT, upper_z_right_flanged.SLDPRT]
